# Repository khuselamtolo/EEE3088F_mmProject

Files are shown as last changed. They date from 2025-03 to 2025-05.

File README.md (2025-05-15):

# EEE3088F_mmProject
## PCB Designs of a power subsystem, intended for a micro-mouse maze-solving robot
This repository is for Group 64's design files for the Micro-mouse Power Subsystem Project, as required by the EEE3088F course from the University of Cape Town.

We, as the students, give our consent for third parties to use, modify, distribute and sell the files found within in repository, but please contact the University of Cape Town for full legal licensing.

Group 64's Student Numbers: MTLKHU009, VRSNEO001

## Repository File Layout
In the main directory of the repository (where this README.md file is) is the main files of the project (.kicad_pro .kicad_sch and .kicad_pcb).
The folder 'jlcpcb' contains the production files, formatted for the manufacturer JLCPCB.
The folders 'Connector_USB.lib' and 'Connector_USB.pretty' contain footprint files for USB connectors, for either Windows or MacOS (respectively). These files are referenced for the USB-C connector in the project.

## How to use
Download the repository, and open the file 'EEE3088F_micro_mouse_power_subsystem.kicad_pro' using Ki_CAD 9.0 or any later version that's compatible with KiCAD 9.0 files.

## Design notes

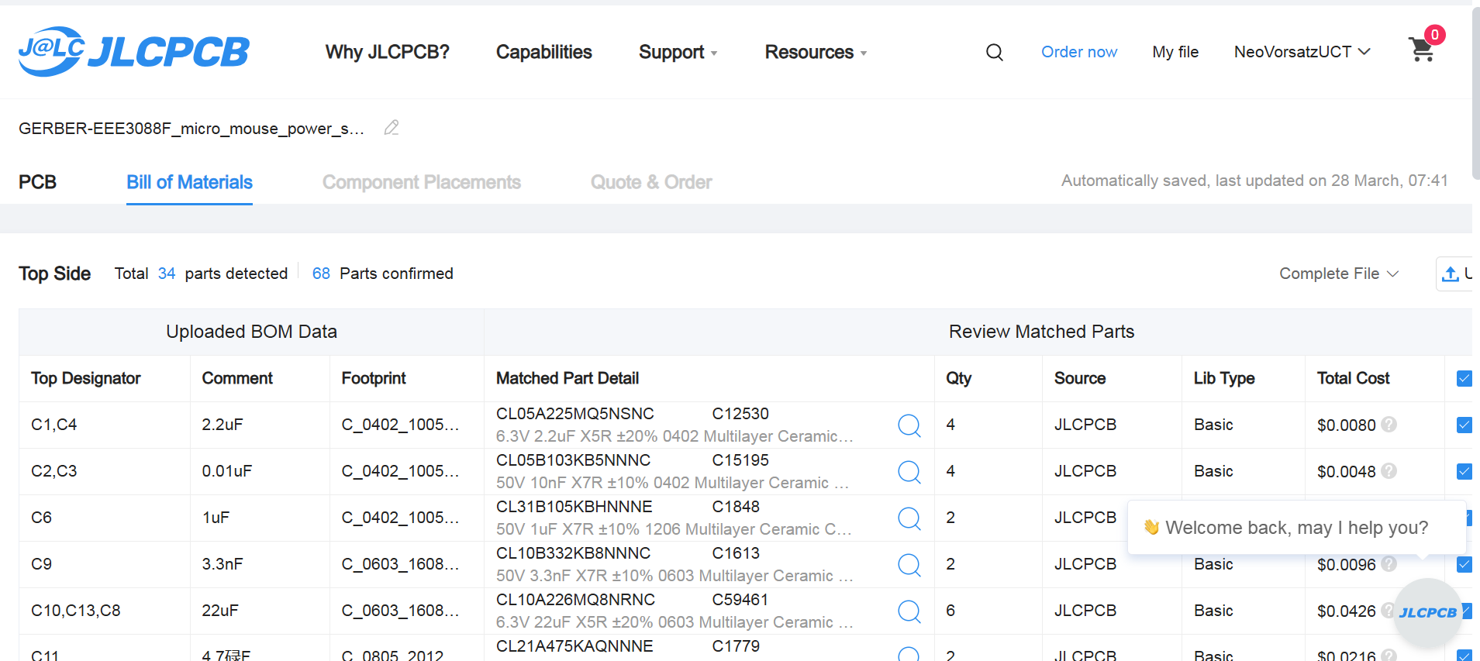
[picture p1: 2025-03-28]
jlcpcb/production_files/EEE3088F_Project_JLCPCBBOM_vrsneo001.png

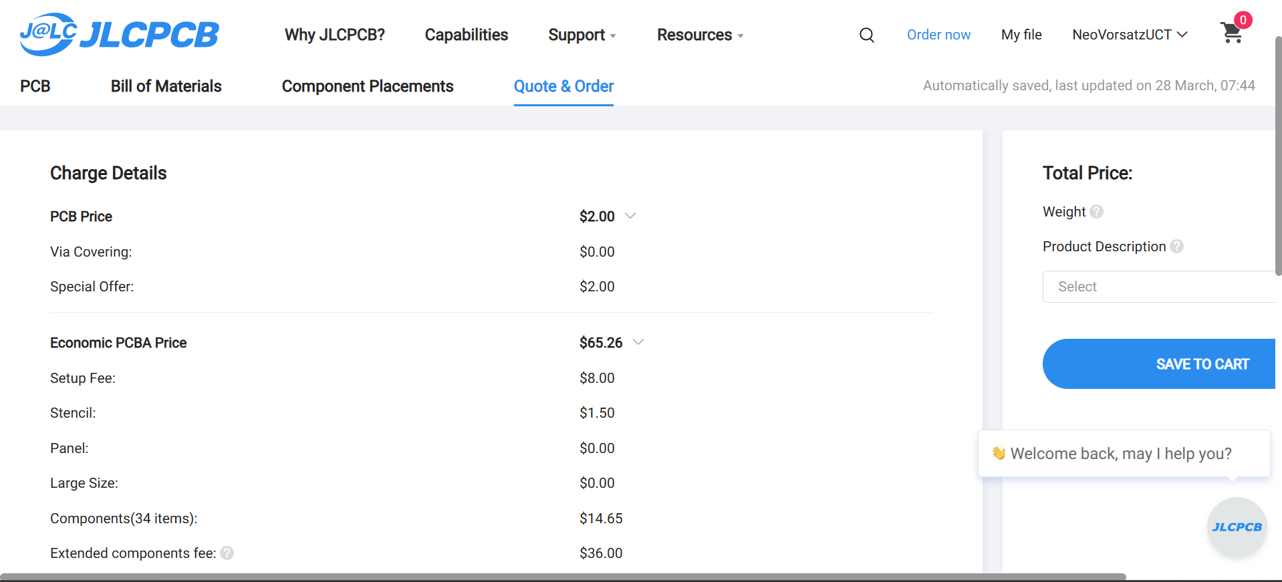
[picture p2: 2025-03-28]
jlcpcb/production_files/EEE3088F_Project_JLCPCBacceptance_vrsneo001.png

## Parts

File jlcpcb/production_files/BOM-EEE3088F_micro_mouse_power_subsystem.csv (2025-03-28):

Comment | Designator | Footprint | LCSC | Quantity
2.2uF | C1,C4 | C_0402_1005Metric | C12530 | 2
TC4426xOA | U4 | SOIC-8_3.9x4.9mm_P1.27mm | C148047 | 1
0.01uF | C2,C3 | C_0402_1005Metric | C15195 | 2
10uF | C12,C7 | C_0402_1005Metric | C15525 | 2
3.3nF | C9 | C_0603_1608Metric | C1613 | 1
100R | R17,R21 | R_0805_2012Metric | C17408 | 2
6.8k | R5 | R_0805_2012Metric | C17772 | 1
4.7µF | C11 | C_0805_2012Metric | C1779 | 1
1uF | C6 | C_0402_1005Metric | C1848 | 1
HX SS12D10G6 | SW2 | SolderWire-0.75sqmm_1x03_P4.8mm_D1.25mm_OD2.3mm | C19189121 | 1
TP4056-42-ESOP8 | U7 | SOIC-8-1EP_3.9x4.9mm_P1.27mm_EP2.41x3.3mm_ThermalVias | C21417 | 1
220kR | R13,R2,R3 | R_0603_1608Metric | C22961 | 3
27kR | R12 | R_0603_1608Metric | C22967 | 1
3.3k | R9 | R_0603_1608Metric | C22978 | 1
1N4734A-TAP | D1 | D_DO-35_SOD27_P2.54mm_Vertical_AnodeUp | C241984 | 1
12kR | R15,R7 | R_0402_1005Metric | C25752 | 2
10k | R10,R11,R18,R8 | R_0603_1608Metric | C25804 | 4
18kR | R14 | R_0603_1608Metric | C25810 | 1
MT3608L | U9 | SOT-23-6 | C2932326 | 1
TPTLV70033DDCR | U8 | SOT-23-5 | C2937039 | 1
USB_C_Receptacle_USB2.0_14P | J3 | USB_C_Receptacle_GCT_USB4125-xx-x-0190_6P_TopMnt_Horizontal | C3151746 | 1
22k | R20 | R_0603_1608Metric | C31850 | 1
20k | R19,R6 | R_0603_1608Metric | C4184 | 2
1k | R16,R22,R23,R4 | R_1206_3216Metric | C4410 | 4
TPS82130 | U6 | Texas_SIL0008D_MicroSiP-8-1EP_2.8x3mm_P0.65mm_EP1.1x1.9mm_ThermalVias | C473914 | 1
CRS08 | D2 | D_1206_3216Metric | C475662 | 1
DRV8833PWPR | U2,U3 | TSSOP-16_4.4x5mm_P0.65mm | C50506 | 2
PMOS | Q1,Q2,Q3 | SOT-23 | C5224173 | 3
4.7uH | L1 | L_1008_2520Metric | C5832360 | 1
22uF | C10,C13,C8 | C_0603_1608Metric | C59461 | 3
1mR | R1 | R_1206_3216Metric | C7419993 | 1
NMOS | Q4 | SOT-23 | C8545 | 1
INA219AIDCNR | U1 | SOT-23-8 | C87469 | 1
CH224K | U5 | SSOP-10-1EP_3.9x4.9mm_P1mm_EP2.1x3.3mm | C970725 | 1

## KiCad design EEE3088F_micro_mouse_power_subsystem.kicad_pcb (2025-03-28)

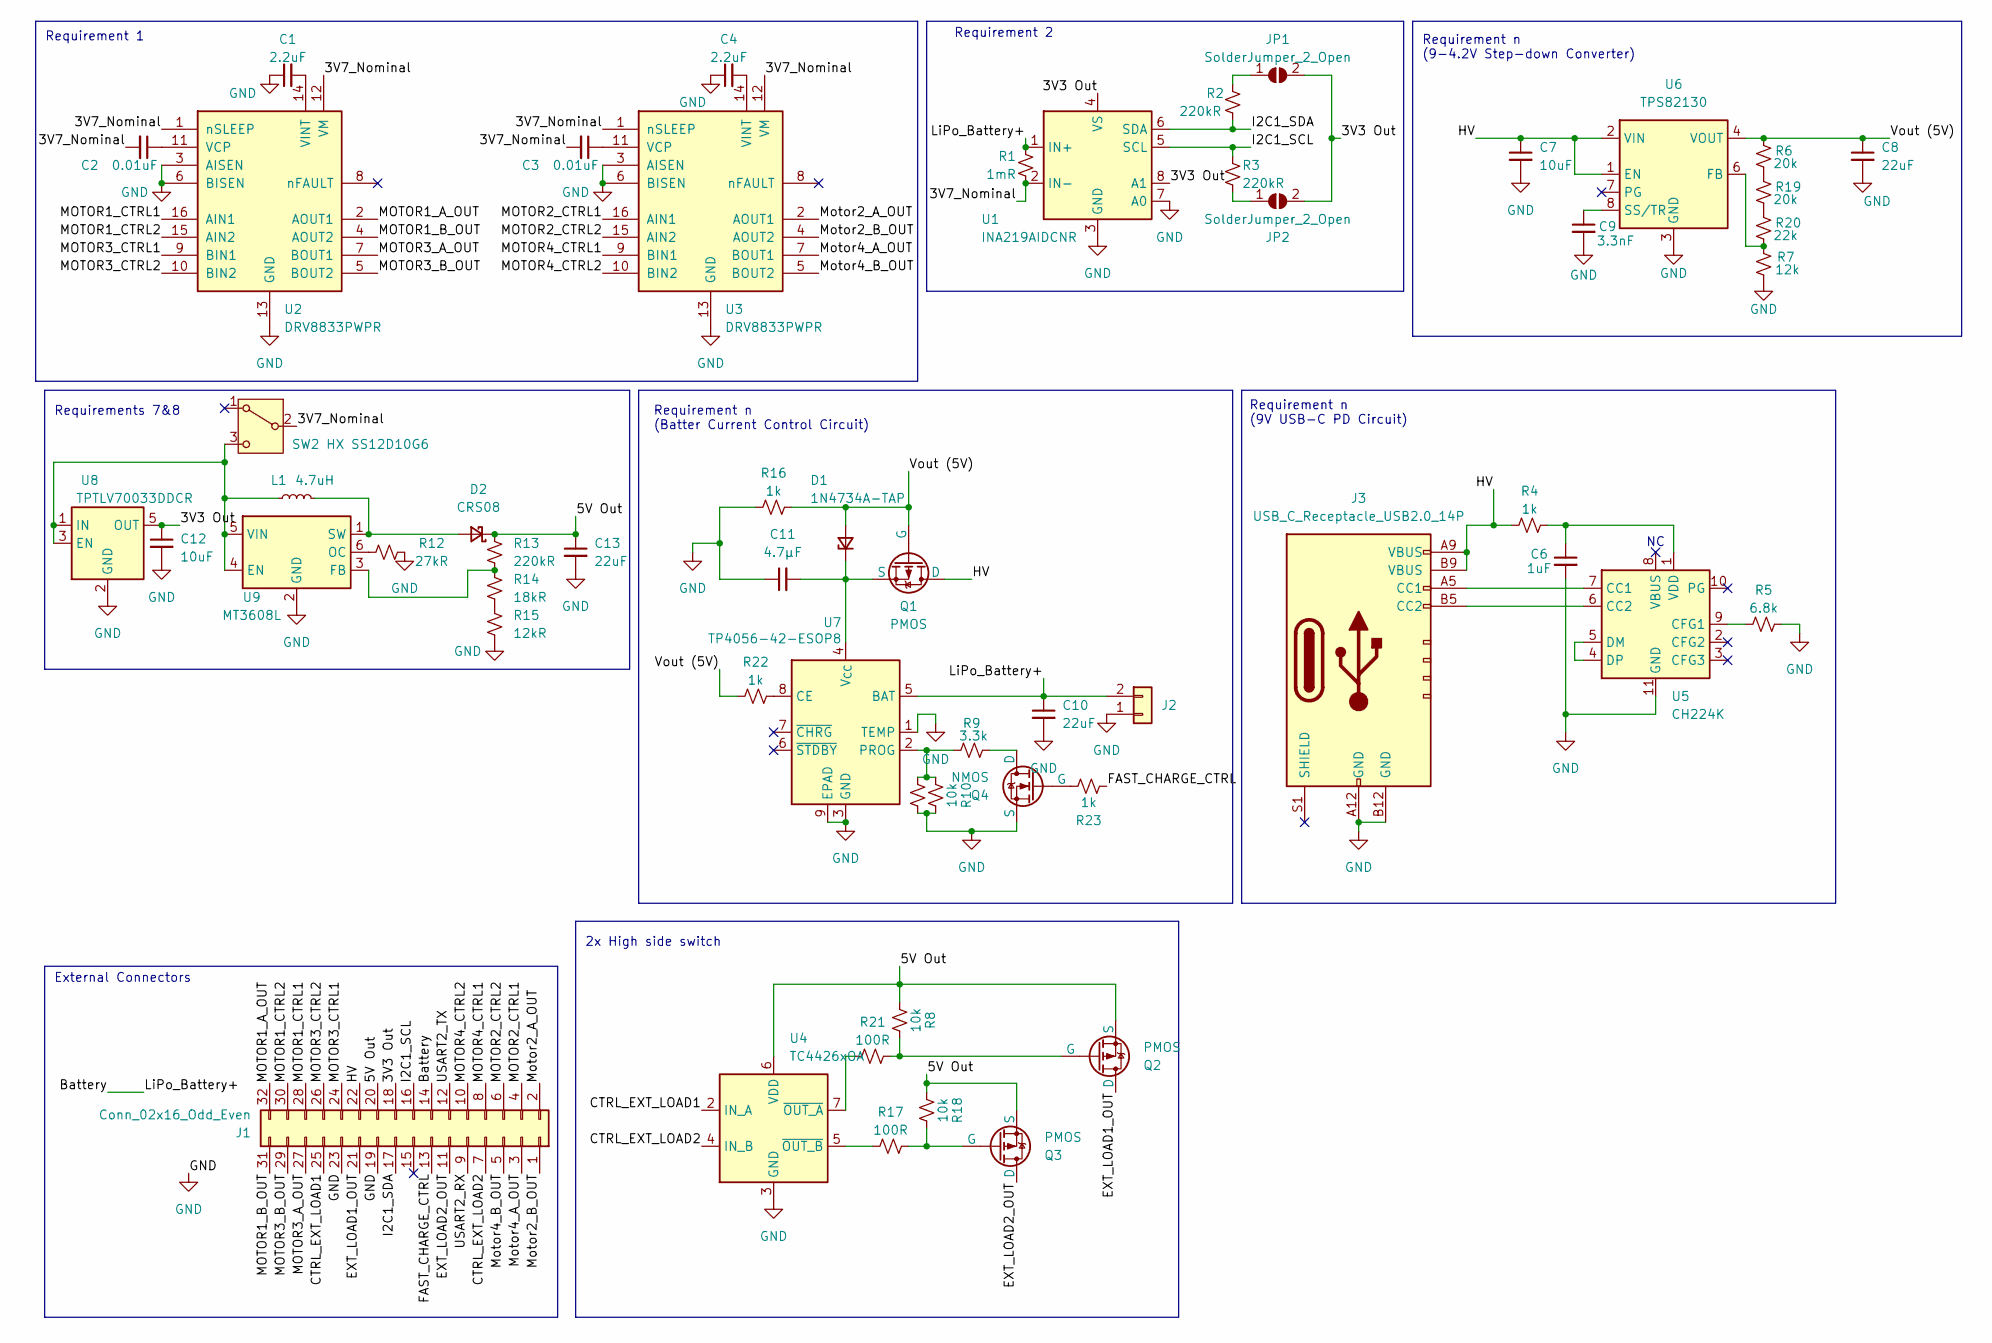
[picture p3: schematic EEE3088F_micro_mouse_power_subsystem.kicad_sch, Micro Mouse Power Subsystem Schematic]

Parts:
C1, C4: 2.2uF; C_0402_1005Metric; LCSC C12530
C2, C3: 0.01uF; C_0402_1005Metric; LCSC C15195
C6: 1uF; C_0402_1005Metric; LCSC C1848
C7, C12: 10uF; C_0402_1005Metric; LCSC C15525
C8, C10, C13: 22uF; C_0603_1608Metric; LCSC C59461
C9: 3.3nF; C_0603_1608Metric; LCSC C1613
C11: 4.7µF; C_0805_2012Metric; LCSC C1779
D1: 1N4734A-TAP; D_DO-35_SOD27_P2.54mm_Vertical_AnodeUp; LCSC C241984
D2: CRS08; D_1206_3216Metric; LCSC C475662
J1: Conn_02x16_Odd_Even; PinHeader_2x16_P2.54mm_Vertical
J2: Conn_01x02; JST_PH_S2B-PH-K_1x02_P2.00mm_Horizontal
J3: USB_C_Receptacle_USB2.0_14P; USB_C_Receptacle_GCT_USB4125-xx-x-0190_6P_TopMnt_Horizontal; LCSC C168701
JP1, JP2: SolderJumper_2_Open; SolderJumper-2_P1.3mm_Open_TrianglePad1.0x1.5mm
L1: 4.7uH; L_1008_2520Metric; LCSC C5832360
Q1, Q2, Q3: PMOS; SOT-23; LCSC C5224173
Q4: NMOS; SOT-23; LCSC C8545
R1: 1mR; R_1206_3216Metric; LCSC C7419993
R2, R3, R13: 220kR; R_0603_1608Metric; LCSC C22961
R4, R16, R22, R23: 1k; R_1206_3216Metric; LCSC C4410
R5: 6.8k; R_0805_2012Metric; LCSC C17772
R6, R19: 20k; R_0603_1608Metric; LCSC C4184
R7: 12k; R_0402_1005Metric; LCSC C25752
R8, R10, R11, R18: 10k; R_0603_1608Metric; LCSC C25804
R9: 3.3k; R_0603_1608Metric; LCSC C22978
R12: 27kR; R_0603_1608Metric; LCSC C22967
R14: 18kR; R_0603_1608Metric; LCSC C25810
R15: 12kR; R_0402_1005Metric; LCSC C25752
R17, R21: 100R; R_0805_2012Metric; LCSC C17408
R20: 22k; R_0603_1608Metric; LCSC C31850
SW2: HX SS12D10G6; SolderWire-0.75sqmm_1x03_P4.8mm_D1.25mm_OD2.3mm; LCSC C19189121
U1: INA219AIDCNR; SOT-23-8; LCSC C87469
U2, U3: DRV8833PWPR; TSSOP-16_4.4x5mm_P0.65mm; LCSC C50506
U4: TC4426xOA; SOIC-8_3.9x4.9mm_P1.27mm
U5: CH224K; SSOP-10-1EP_3.9x4.9mm_P1mm_EP2.1x3.3mm; LCSC C970725
U6: TPS82130; Texas_SIL0008D_MicroSiP-8-1EP_2.8x3mm_P0.65mm_EP1.1x1.9mm_T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; LCSC C473914
U7: TP4056-42-ESOP8; SOIC-8-1EP_3.9x4.9mm_P1.27mm_EP2.41x3.3mm_ThermalVias; LCSC C21417
U8: TPTLV70033DDCR; SOT-23-5; LCSC C2937039
U9: MT3608L; SOT-23-6; LCSC C2932326

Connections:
/3V3 Out: C12.1, J1.18, JP1.2 (B), JP2.2 (B), U1.4 (VS), U1.8 (A1), U8.5 (OUT)
/3V7_Nominal: C2.2, C3.2, R1.2, SW2.2 (B), U1.2 (IN-), U2.1 (nSLEEP), U2.12 (VM), U3.1 (nSLEEP), U3.12 (VM)
/5V Out: C13.1, D2.1 (K), J1.20, Q2.3 (S), Q3.3 (S), R8.1, R13.1, R18.1, U4.6 (VDD)
/Battery: C10.1, J1.14, J2.2 (Pin_1), R1.1, U1.1 (IN+), U7.5 (BAT)
/CTRL_EXT_LOAD1: J1.25, U4.2 (IN_A)
/CTRL_EXT_LOAD2: J1.7, U4.4 (IN_B)
/EXT_LOAD1_OUT: J1.21, Q2.1 (D)
/EXT_LOAD2_OUT: J1.11, Q3.1 (D)
/FAST_CHARGE_CTRL: J1.13, R23.2
/HV: C7.1, J1.22, J3.A9 (VBUS), J3.B4 (VBUS), J3.B9 (VBUS), Q1.1 (D), R4.2, U6.1 (EN), U6.2 (VIN)
/I2C1_SCL: J1.16, R3.1, U1.5 (SCL)
/I2C1_SDA: J1.17, R2.2, U1.6 (SDA)
/MOTOR1_A_OUT: J1.32, U2.2 (AOUT1)
/MOTOR1_B_OUT: J1.31, U2.4 (AOUT2)
/MOTOR1_CTRL1: J1.28, U2.16 (AIN1)
/MOTOR1_CTRL2: J1.30, U2.15 (AIN2)
/MOTOR2_CTRL1: J1.4, U3.16 (AIN1)
/MOTOR2_CTRL2: J1.6, U3.15 (AIN2)
/MOTOR3_A_OUT: J1.27, U2.7 (BOUT1)
/MOTOR3_B_OUT: J1.29, U2.5 (BOUT2)
/MOTOR3_CTRL1: J1.24, U2.9 (BIN1)
/MOTOR3_CTRL2: J1.26, U2.10 (BIN2)
/MOTOR4_CTRL1: J1.8, U3.9 (BIN1)
/MOTOR4_CTRL2: J1.10, U3.10 (BIN2)
/Motor2_A_OUT: J1.2, U3.2 (AOUT1)
/Motor2_B_OUT: J1.1, U3.4 (AOUT2)
/Motor4_A_OUT: J1.3, U3.7 (BOUT1)
/Motor4_B_OUT: J1.5, U3.5 (BOUT2)
/USART2_RX: J1.9
/USART2_TX: J1.12
/Vout (5V): C8.1, D1.2 (A), Q1.2 (G), R6.1, R16.1, R22.2, U6.4 (VOUT), U6.5 (VOUT)
GND: C1.1, C4.1, C6.2, C7.2, C8.2, C9.2, C10.2, C11.1, C12.2, C13.2, J1.19, J1.23, J2.1 (Pin_2), J3.A12 (GND), J3.B1 (GND), J3.B12 (GND), Q4.3 (S), R5.2, R7.2, R10.2, R11.2, R12.2, R15.2, R16.2, U1.3 (GND), U1.7 (A0), U2.3 (AISEN), U2.6 (BISEN), U2.13 (GND), U3.3 (AISEN), U3.6 (BISEN), U3.13 (GND), U4.3 (GND), U5.11 (GND), U6.3 (GND), U6.9 (GND), U7.1 (TEMP), U7.3 (GND), U7.9 (EPAD), U8.2 (GND), U8.4 (GND), U9.2 (GND)
unnamed: C11.2, D1.1 (K), Q1.3 (S), U7.4 (V_{CC})
unnamed: D2.2 (A), L1.2, U9.1 (SW)
unnamed: J3.A5 (CC1), U5.7 (CC1)
unnamed: J3.B5 (CC2), U5.6 (CC2)
unnamed: JP1.1 (A), R2.1
unnamed: JP2.1 (A), R3.2
unnamed: Q2.2 (G), R8.2, R21.2
unnamed: Q3.2 (G), R17.2, R18.2
unnamed: Q4.1 (D), R9.2
unnamed: Q4.2 (G), R23.1
unnamed: R14.2, R15.1
unnamed: R6.2, R19.1
unnamed: R19.2, R20.1
unnamed: L1.1, SW2.3 (C), U8.1 (IN), U8.3 (EN), U9.4 (EN), U9.5 (VIN)
unnamed: C2.1, U2.11 (VCP)
unnamed: C1.2, U2.14 (VINT)
unnamed: C3.1, U3.11 (VCP)
unnamed: C4.2, U3.14 (VINT)
unnamed: R21.1, U4.7 (~OUT_A)
unnamed: R17.1, U4.5 (~OUT_B)
unnamed: R5.1, U5.9 (CFG1)
unnamed: U5.4 (DP), U5.5 (DM)
unnamed: C6.1, R4.1, U5.1 (VDD)
unnamed: R7.1, R20.2, U6.6 (FB)
unnamed: C9.1, U6.8 (SS/TR)
unnamed: R22.1, U7.8 (CE)
unnamed: R9.1, R10.1, R11.1, U7.2 (PROG)
unnamed: R13.2, R14.1, U9.3 (FB)
unnamed: R12.1, U9.6 (OC)

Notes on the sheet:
Requirement n (9-4.2V Step-down Converter)
Requirement n (9V USB-C PD Circuit)
2x High side switch
Requirement 1
Requirement n (Batter Current Control Circuit)
Requirements 7&8
External Connectors
Requirement 2

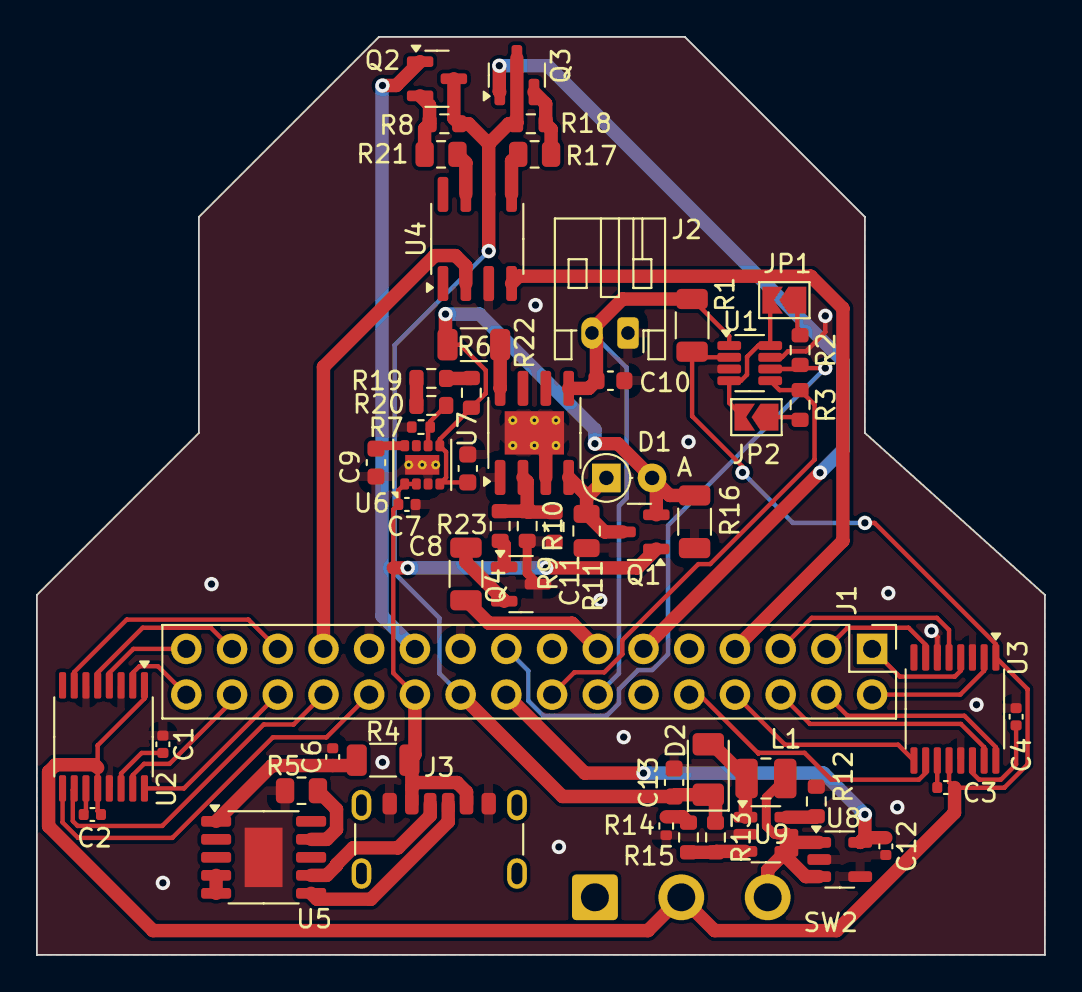
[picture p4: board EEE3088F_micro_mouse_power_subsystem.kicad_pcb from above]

Board: 2 copper layers, 56.0 x 51.0 mm, 57 parts (0 on the bottom side), 59 nets.

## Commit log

2025-03-24 Added KiCad project with 02x16 pins
    [EEE3088F_micro_mouse_power_subsystem.kicad_pcb, EEE3088F_micro_mouse_power_subsystem.kicad_sch]
2025-03-25 Added circuit for Requirement 2
    [EEE3088F_micro_mouse_power_subsystem.kicad_sch]
2025-03-25 Added circuit for Requirement 1
    [EEE3088F_micro_mouse_power_subsystem.kicad_sch]
2025-03-25 test commit
    Just testing
    [EEE3088F_micro_mouse_power_subsystem.kicad_sch]
2025-03-25 Updated LCSC numbers and Requirements 7 and 8
    [EEE3088F_micro_mouse_power_subsystem.kicad_sch]
2025-03-25 Battery charging circuitry added
    [EEE3088F_micro_mouse_power_subsystem.kicad_sch]
2025-03-25 Added circuits for requirements 7 and 8
    [EEE3088F_micro_mouse_power_subsystem.kicad_sch]
2025-03-26 Minor updates after meeting
    [EEE3088F_micro_mouse_power_subsystem.kicad_sch]
2025-03-27 Added footprints for half of the components
    [EEE3088F_micro_mouse_power_subsystem.kicad_sch]
2025-03-27 Final changes to schematic and footprints
    [EEE3088F_micro_mouse_power_subsystem.csv, EEE3088F_micro_mouse_power_subsystem.kicad_sch]
2025-03-28 Created PCB layout and production files
    [BOM-EEE3088F_micro_mouse_power_subsystem.csv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]
2025-05-15 Deleted unnecessary files, like the back up files and cache
    [EEE3088F_micro_mouse_power_subsystem.csv]
